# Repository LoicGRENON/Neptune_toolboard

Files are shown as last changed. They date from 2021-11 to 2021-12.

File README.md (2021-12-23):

# Neptune CAN Toolboard

A small controller board designed to be used on a 3D printer as well as a SMD Pick and Place (PNP) machine.
It is designed to be used with Klipper firmware using CAN bus or USB connection.
Using CAN bus is it possible to chain many board using a pair of twisted wires for data and power.
It is also a good solution to simplify the toolhead wiring as only one cable is needed.

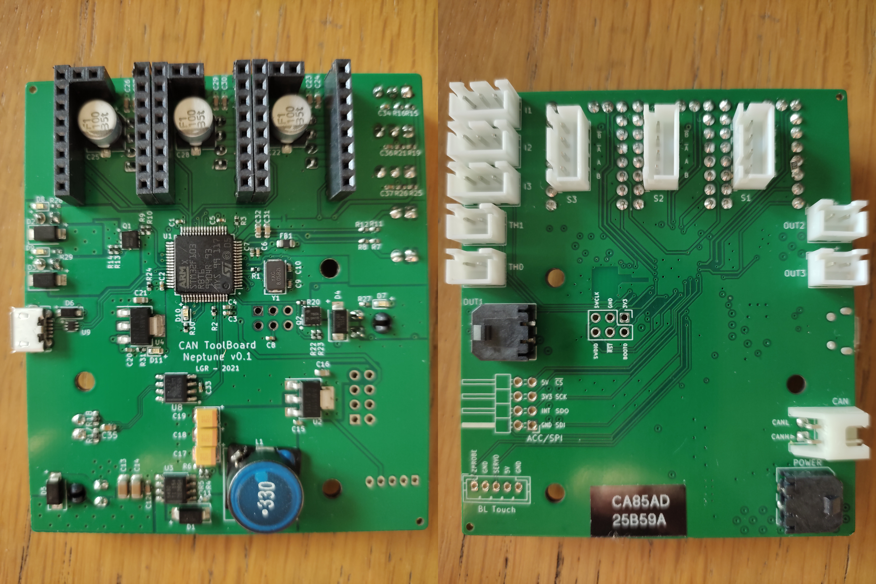
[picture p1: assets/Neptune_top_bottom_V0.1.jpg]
Neptune toolboard top and bottom sides


## Features:

* STM32F103 72MHz 32bits ARM MCU
* CAN bus
* USB (micro USB type B connector)
* 3x stepstick drivers with UART communication (with full diagnostics and control)
* 3x 5V powered inputs (endstop, filament runout sensor or whatever)
* 2x thermistor inputs (2.2k pullup resistor for PT1000 support)
* 3x MOSFET outputs (with freewheeling diode) - up to 5A
* 1x BL Touch connector
* 1x port for accelerometer connection for input shaping (no onboard chip as keeping the accelerometer as close to the nozzle is better)
* LEDs (Power, mosfet outputs & Activity)
* Debug port with SWD, NRST and BOOT0
* Components choosen for high-temp environnement (up to 85°C)

## Getting started:

To be defined

## Attribution

This board was designed from scratch but inspired by the [Huvud] and [TurboCAN] boards.

[Huvud]: https://github.com/bondus/KlipperToolboard
[TurboCAN]: https://github.com/henrikssn/TurboCAN

## License:
All included files are licensed under the [GNU GPL-3 license].

[GNU GPL-3 license]: https://www.gnu.org/licenses/gpl-3.0.html

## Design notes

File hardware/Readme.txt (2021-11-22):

kikit fab jlcpcb --assembly --schematic Toolboard/hardware_V6/TriStepToolboard.sch Toolboard/hardware_V6/TriStepToolboard.kicad_pcb Toolboard/hardware_V6/assembly

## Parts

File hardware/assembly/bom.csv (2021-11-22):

Comment | Designator | Footprint | LCSC
Debug | J1 | Connector_PinHeader_2.54mm:PinHeader_2x03_P2.54mm_Vertical | ---
12p | C9,C10 | Capacitor_SMD:C_0402_1005Metric | C1547
10k | R2,R3,R4,R8,R12,R10,R14,R22,R29,R28,R27,R19,R21,R15,R16,R25,R26 | Resistor_SMD:R_0402_1005Metric | C25744
0.1u | C8,C3,C1,C5,C2,C36,C34,C33,C37 | Capacitor_SMD:C_0402_1005Metric | C1525
Net-Tie_GND_GNDA | NT1 | NetTie:NetTie-2_SMD_Pad0.5mm | ---
1u | C7 | Capacitor_SMD:C_0402_1005Metric | C52923
4.7u | C4,C15,C20 | Capacitor_SMD:C_0402_1005Metric | C23733
10n | C6,C11 | Capacitor_SMD:C_0402_1005Metric | C15195
600 @ 100MHz | FB1 | Inductor_SMD:L_0805_2012Metric | C1017
0 | R1 | Resistor_SMD:R_0402_1005Metric | C17168
8MHz | Y1 | Crystal:Crystal_SMD_5032-2Pin_5.0x3.2mm | C115962
STM32F103R8Tx | U1 | Package_QFP:LQFP-64_10x10mm_P0.5mm | ---
AMS1117-5.0 | U2 | Package_TO_SOT_SMD:SOT-223-3_TabPin2 | C6187
22u | C16,C21 | Capacitor_SMD:C_0603_1608Metric | C59461
AMS1117-3.3 | U4 | Package_TO_SOT_SMD:SOT-223-3_TabPin2 | C6186
SS54 | D1,D5,D2,D3,D4 | Diode_SMD:D_SMA | C22452
33u | L1 | Inductor_SMD:L_12x12mm_H8mm | C87568
TPS5430DDAR | U3 | Package_SO:TI_SO-PowerPAD-8_ThermalVias | C9864
10u | C14,C13 | Capacitor_SMD:C_1206_3216Metric | C13585
0.1u | C12,C26,C29,C23,C24,C27,C30 | Capacitor_SMD:C_0603_1608Metric | C14663
1k | R5 | Resistor_SMD:R_0402_1005Metric | C11702
22u | C17,C18,C19 | Capacitor_Tantalum_SMD:CP_EIA-3528-15_AVX-H | C308917
100 | R6 | Resistor_SMD:R_0402_1005Metric | C25076
TMC2209StepStick | U5,U6,U7 | project:TMC2209StepStick | ~
Stepper1 | J2 | Connector_JST:JST_XH_B4B-XH-A_1x04_P2.50mm_Vertical | ---
100uF | C25,C28,C22 | Capacitor_SMD:CP_Elec_6.3x5.8 | C249982
Stepper2 | J3 | Connector_JST:JST_XH_B4B-XH-A_1x04_P2.50mm_Vertical | ---
Stepper3 | J4 | Connector_JST:JST_XH_B4B-XH-A_1x04_P2.50mm_Vertical | ---
GN | D10,D11,D9,D8,D7 | LED_SMD:LED_0603_1608Metric | C72043
470 | R30,R31 | Resistor_SMD:R_0402_1005Metric | C25117
1.5k | R24 | Resistor_SMD:R_0402_1005Metric | C25867
2.2k 0.1% | R7,R11 | Resistor_SMD:R_0402_1005Metric | C186333
2.2u | C31,C32 | Capacitor_SMD:C_0603_1608Metric | C23630
TH0 | J6 | Connector_JST:JST_XH_B2B-XH-A_1x02_P2.50mm_Vertical | ---
TH1 | J7 | Connector_JST:JST_XH_B2B-XH-A_1x02_P2.50mm_Vertical | ---
22 | R9,R13,R20,R23 | Resistor_SMD:R_0402_1005Metric | C25092
FAN0 | J5 | Connector_JST:JST_XH_B2B-XH-A_1x02_P2.50mm_Vertical | ---
FAN1 | J8 | Connector_JST:JST_XH_B2B-XH-A_1x02_P2.50mm_Vertical | ---
HEAT | J11 | Connector_Molex:Molex_Micro-Fit_3.0_43650-0200_1x02_P3.00mm_Horizontal | ---
AON7804 | Q1,Q2 | project:DFN3X3A_Dual | C431197
BL_Touch | J16 | Connector_JST:JST_PH_B5B-PH-K_1x05_P2.00mm_Vertical | ---
Conn_01x03 | J12,J9,J15 | Connector_JST:JST_XH_B3B-XH-A_1x03_P2.50mm_Vertical | ---
PWR | J13 | Connector_Molex:Molex_Micro-Fit_3.0_43650-0200_1x02_P3.00mm_Horizontal | ---
USB_B_Micro | J14 | Connector_USB:USB_Micro-B_Molex-105017-0001 | C10418
USBLC6-2P6 | U9 | Package_TO_SOT_SMD:SOT-666 | C15999
TCAN337DR | U8 | Package_SO:SOIC-8_3.9x4.9mm_P1.27mm | ---
CAN | J10 | Connector_JST:JST_XH_S2B-XH-A_1x02_P2.50mm_Horizontal | ---
B5819W SL | D6 | Diode_SMD:D_SOD-123 | C8598
MountingHole | H1,H2,H3 | MountingHole:MountingHole_3.2mm_M3 | ---
SPI | J17 | Connector_PinHeader_2.54mm:PinHeader_2x04_P2.54mm_Horizontal | ---
60 | R17,R18 | Resistor_SMD:R_0603_1608Metric | C166918
4.7n | C35 | Capacitor_SMD:C_0603_1608Metric | C53987

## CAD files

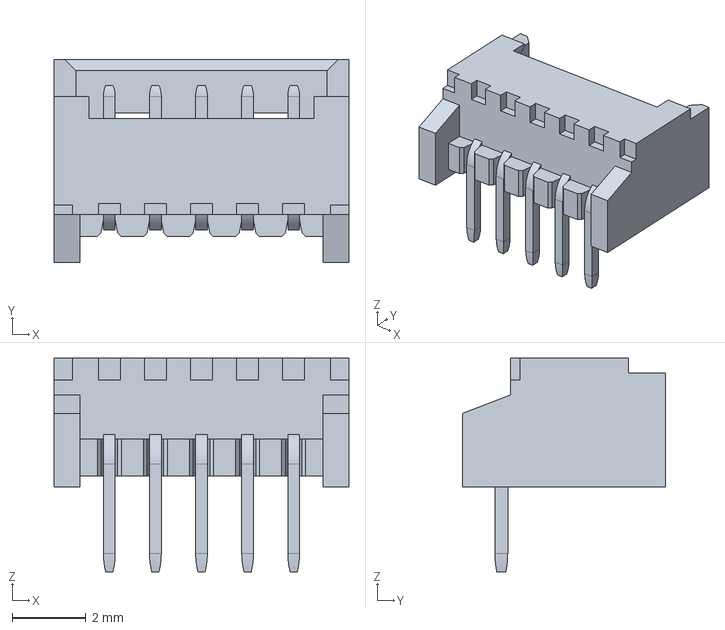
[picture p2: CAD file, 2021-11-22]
hardware/step files/Molex_530480510.stp
8.00 x 5.50 x 5.80 mm

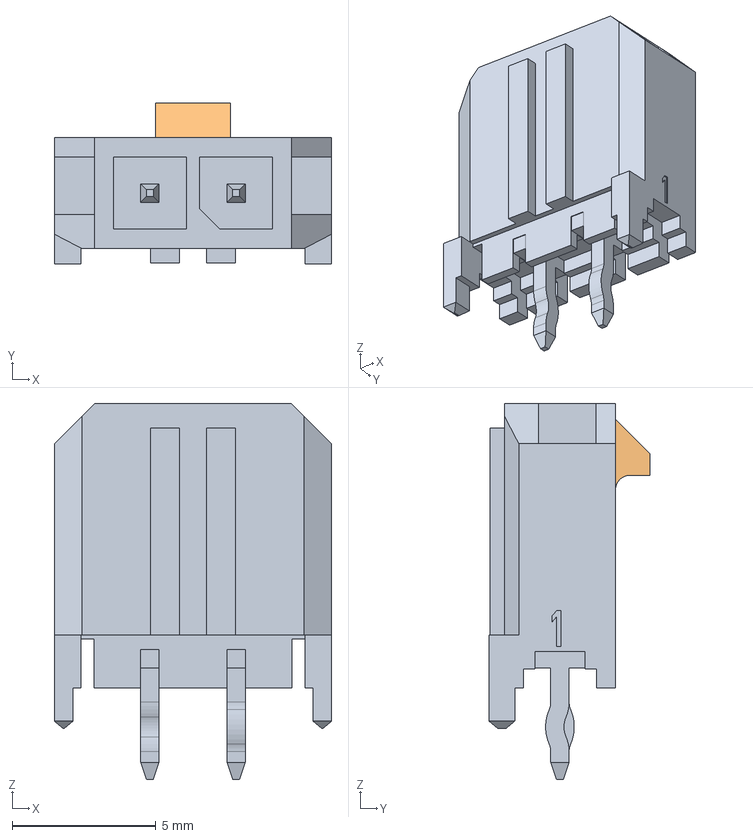
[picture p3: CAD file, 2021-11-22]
hardware/step files/Molex_436500215.stp
9.65 x 5.61 x 13.1 mm

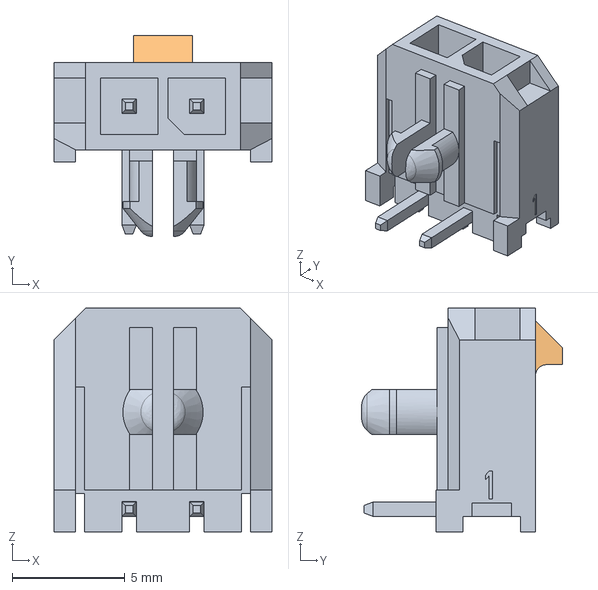
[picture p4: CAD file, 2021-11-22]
hardware/step files/Molex_436500200.stp
9.65 x 8.90 x 9.90 mm

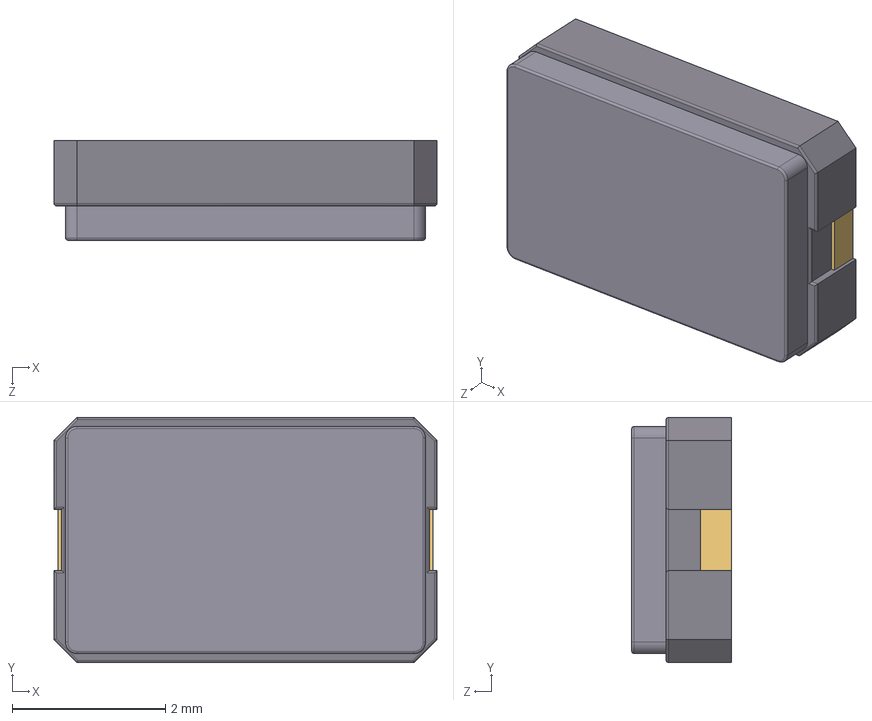
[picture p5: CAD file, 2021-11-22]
hardware/step files/Cystal_5032.step
5.00 x 3.20 x 1.30 mm

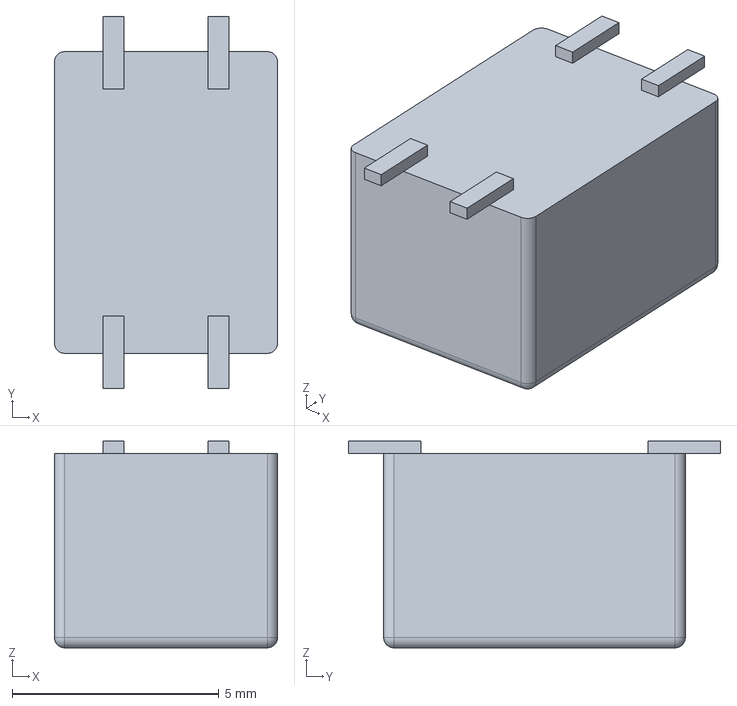
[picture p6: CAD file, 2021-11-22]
hardware/step files/dr331.stp
5.40 x 9.00 x 5.00 mm

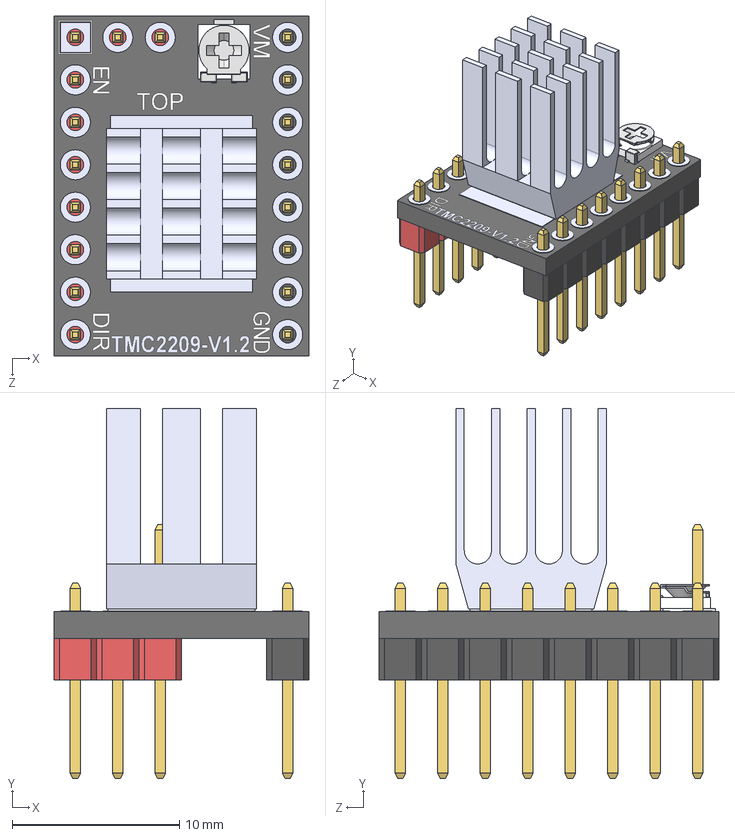
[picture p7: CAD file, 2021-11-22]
hardware/step files/TMC2209-V1.2.STEP
15.2 x 22.1 x 20.3 mm
TMC2209_board^BTT TMC2209-V1.2(2)_BTT TMC2209-V1.2_DＧaut
Pin_Header_1x2_red^BTT TMC2209-V1.2(2)_BTT TMC2209-V1.2_DＧaut
Pin_Header_1x8_red^BTT TMC2209-V1.2(2)_BTT TMC2209-V1.2_DＧaut
Pin_Header_1x8_black^BTT TMC2209-V1.2(2)_BTT TMC2209-V1.2_DＧaut
EVM-3E___ _________^BTT TMC2209-V1.2(2)_BTT TMC2209-V1.2_DＧaut
TMC2209_heatsink^BTT TMC2209-V1.2(2)_BTT TMC2209-V1.2_DＧaut

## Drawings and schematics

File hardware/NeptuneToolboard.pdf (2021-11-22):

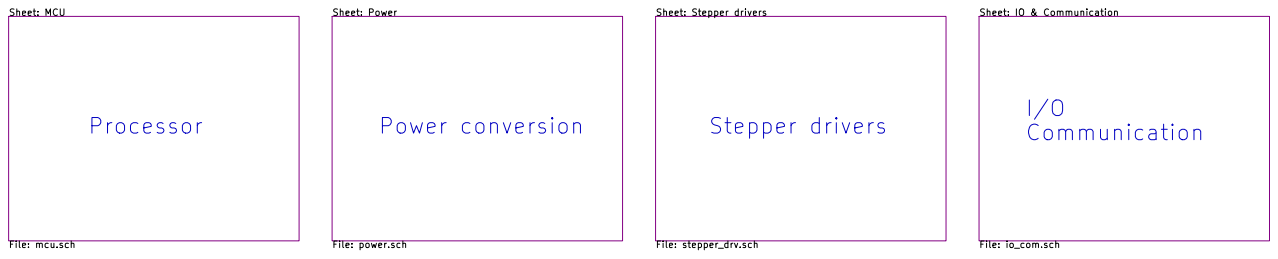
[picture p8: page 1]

File: TriStepToolboard.sch Sheet: / LGR

Id: 1/5 Title: Tri-steppers CAN Tool Board

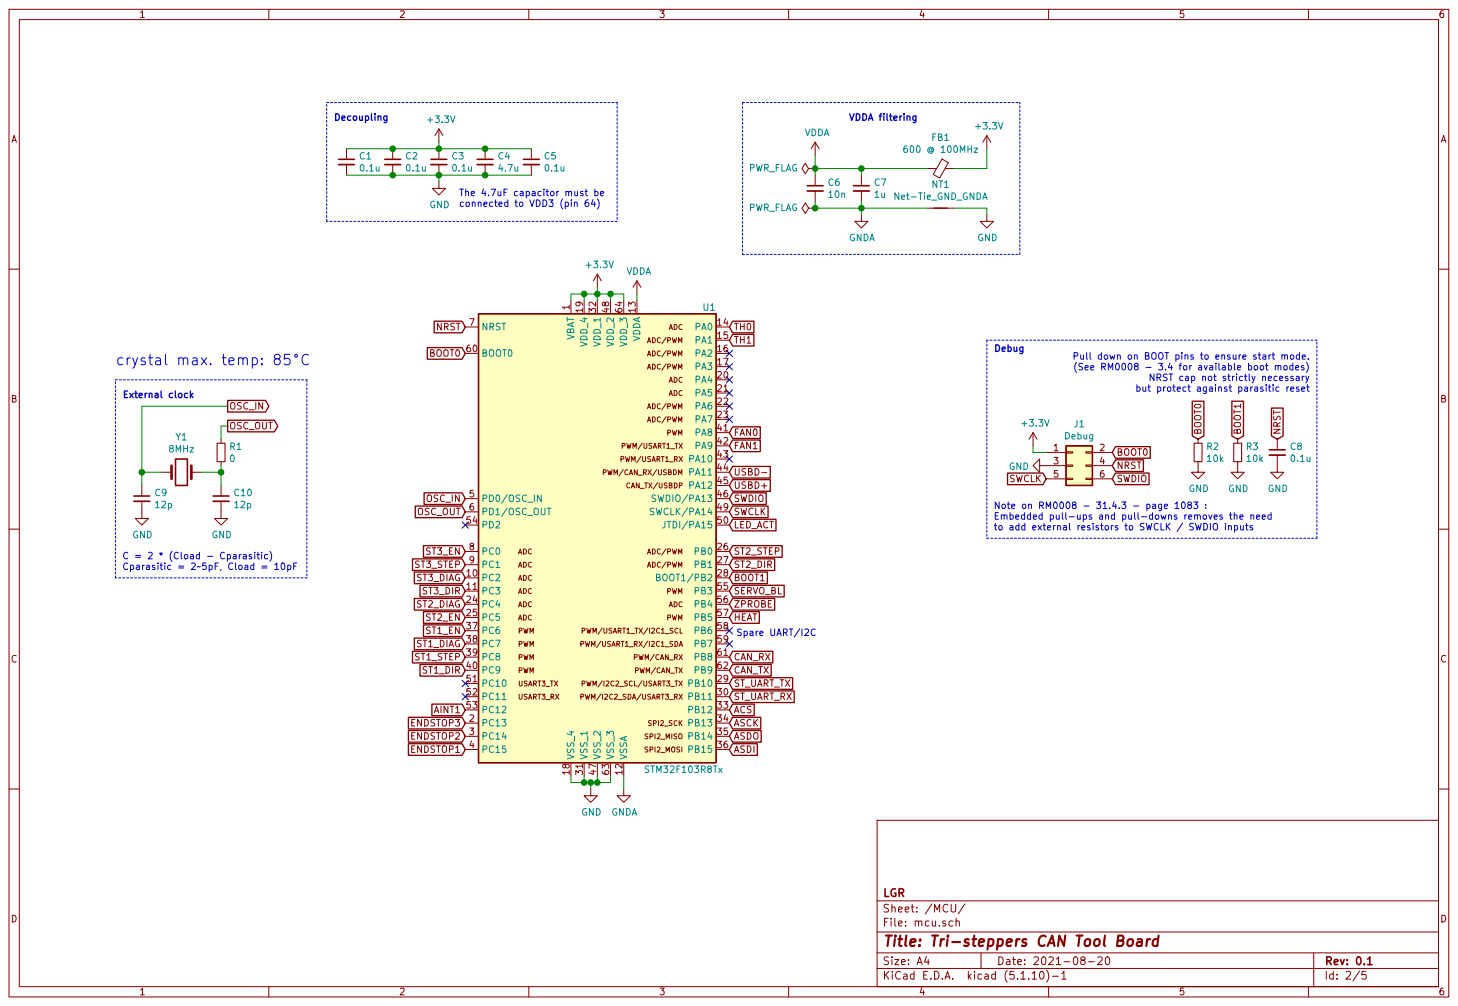
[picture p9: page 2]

1 PC2 10 PC3 11 VSSA 12 VDDA 13 PA0 14 PA1 15 PA2 16 PA3 17 VSS_4 18 VDD_4 19 PC13 2 PA4 20 PA5 21 PA6 22 PA7 23 PC4 24 PC5 25 PB0 26 PB1 27 BOOT1/PB2 28 PB10 29 PC14 3 PB11 30 VSS_1 31 VDD_1 32 PB12 33 PB13 34 PB14 35 PB15 36 PC6 37 PC7 38 PC8 39 PC15 4 PC9 40 PA8 41 PA9 42 PA10 43 PA11 44 PA12 45 SWDIO/PA13 46 VSS_2 47 VDD_2 48 SWCLK/PA14 49 PD0/OSC_IN 5

Pull down on BOOT pins to ensure start mode.
(See RM0008 - 3.4 for available boot modes)

NRST cap not strictly necessary
but protect against parasitic reset

Note on RM0008 - 31.4.3 - page 1083 :
Embedded pull-ups and pull-downs removes the need
to add external resistors to SWCLK / SWDIO inputs

File: mcu.sch Sheet: /MCU/ LGR

Id: 2/5 Title: Tri-steppers CAN Tool Board

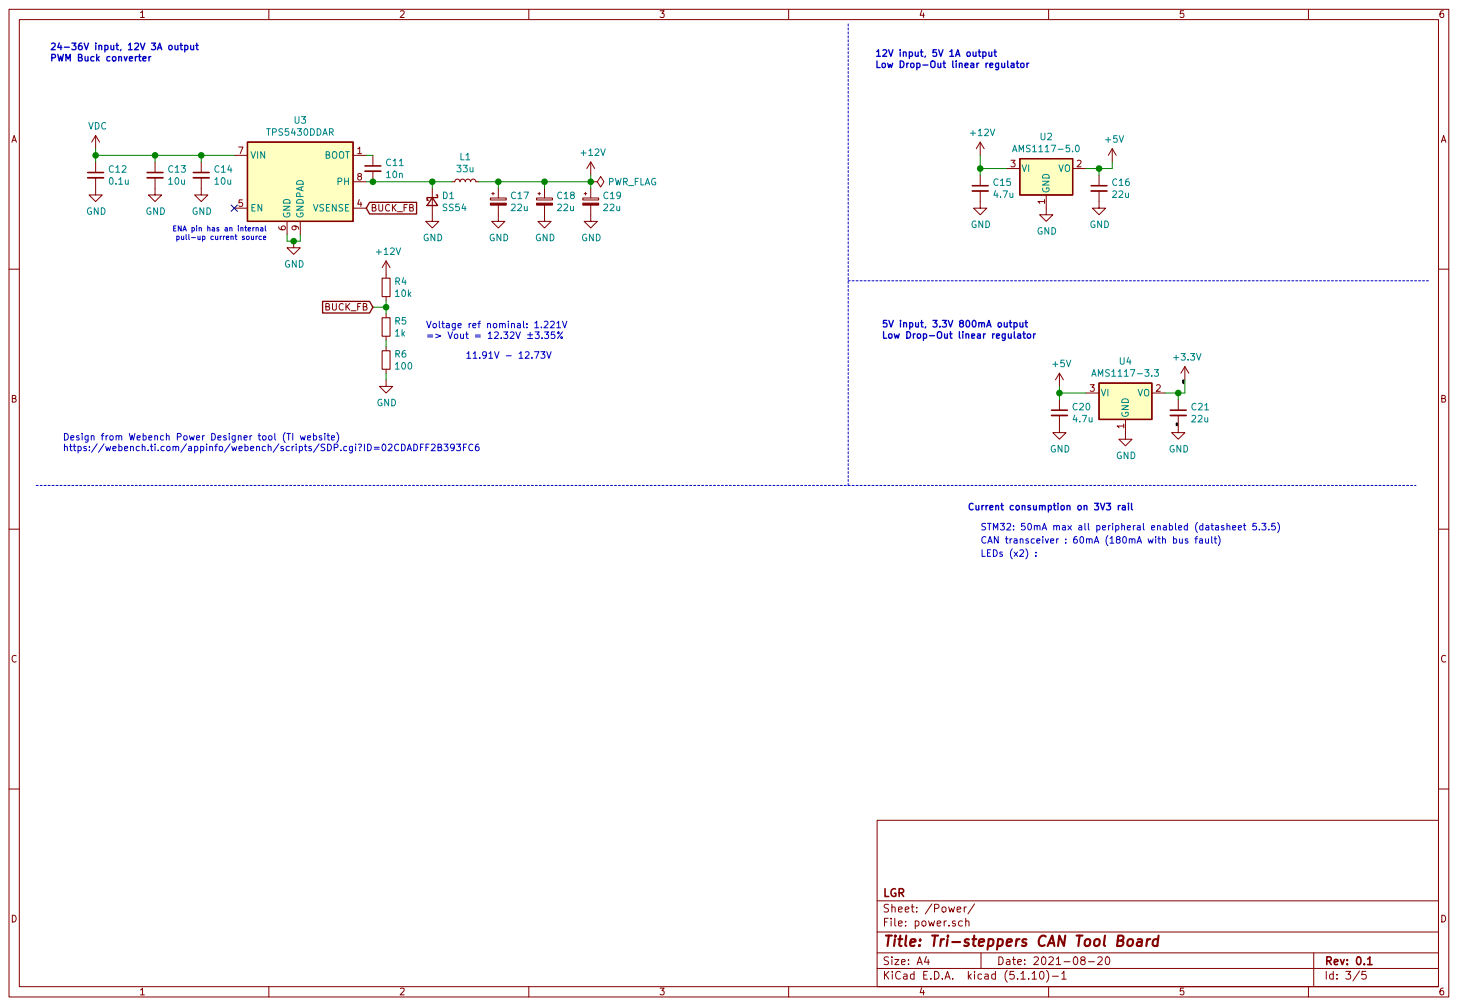
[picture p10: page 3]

12V input, 5V 1A output
Low Drop-Out linear regulator

1 VO 2 VI 3 U4 AMS1117-3.3 GND GND GND

Design from Webench Power Designer tool (TI website)
https://webench.ti.com/appinfo/webench/scripts/SDP.cgi?ID=02CDADFF2B393FC6

Current consumption on 3V3 rail
STM32: 50mA max all peripheral enabled (datasheet 5.3.5)

File: power.sch Sheet: /Power/ LGR

Id: 3/5 Title: Tri-steppers CAN Tool Board

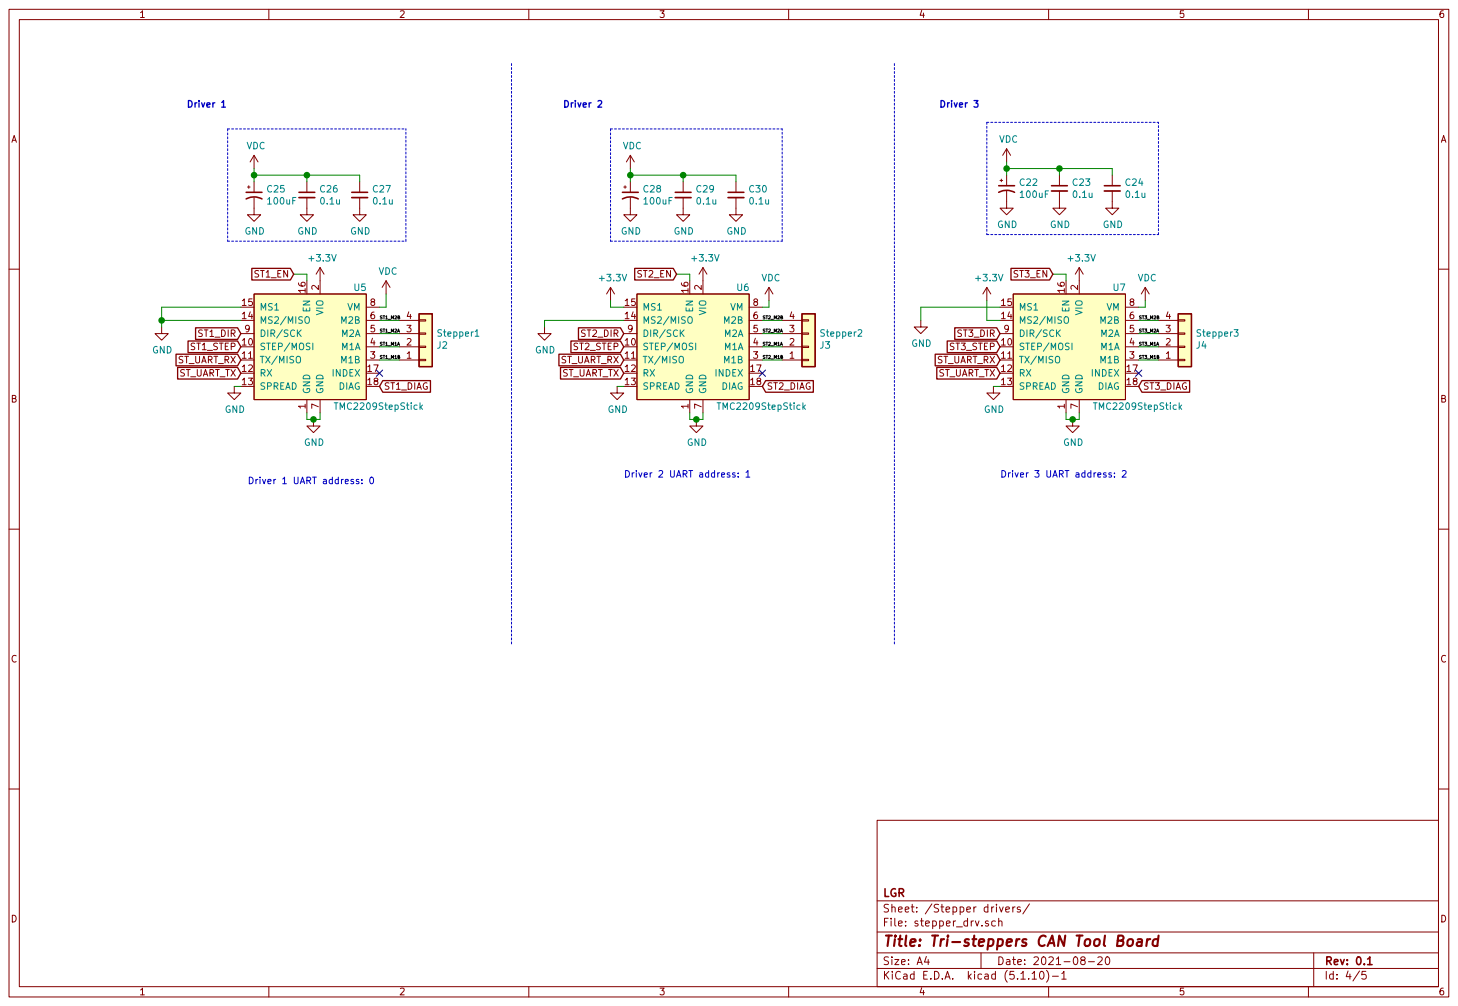
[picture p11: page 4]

7 VM 8 DIR/SCK 9 U6 TMC2209StepStick GND GND GND GND

7 VM 8 DIR/SCK 9 U5 GND TMC2209StepStick GND GND

1 STEP/MOSI 10 TX/MISO 11 RX 12 SPREAD 13 MS2/MISO 14 MS1 15 EN 16

7 VM 8 DIR/SCK 9 U7 TMC2209StepStick GND

Sheet: /Stepper drivers/ LGR

File: stepper_drv.sch
Id: 4/5 Title: Tri-steppers CAN Tool Board

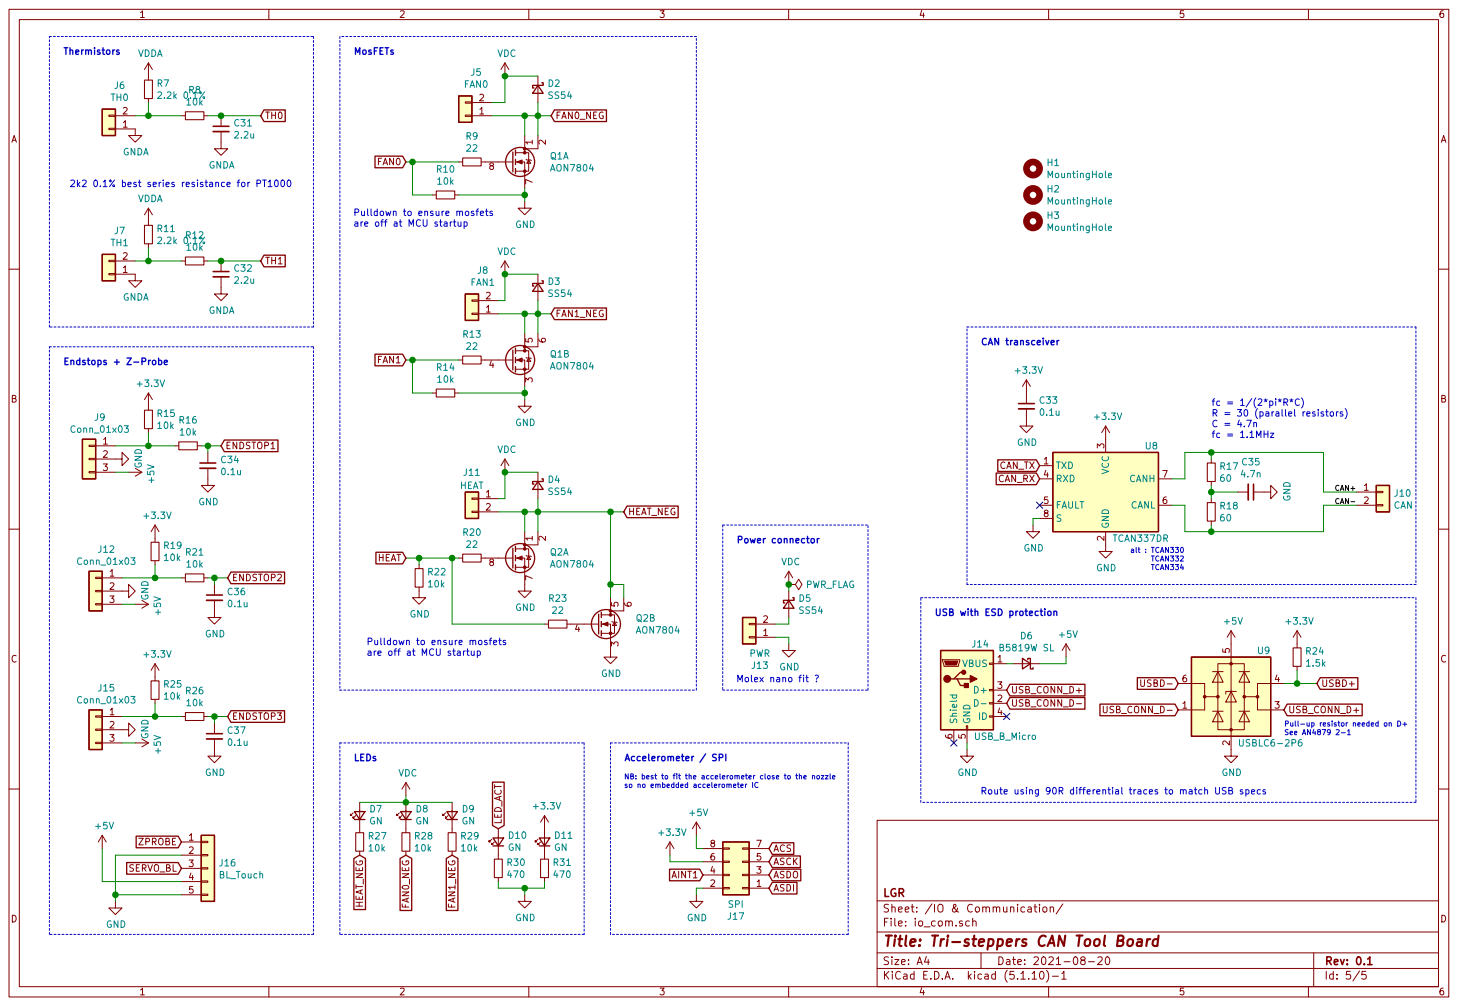
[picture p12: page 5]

CAN+ CAN- Pulldown to ensure mosfets are off at MCU startup

3 RXD 4 FAULT 5 CANL 6 CANH 7 S

so no embedded accelerometer IC

File: io_com.sch Sheet: /IO & Communication/ LGR

Id: 5/5 Title: Tri-steppers CAN Tool Board

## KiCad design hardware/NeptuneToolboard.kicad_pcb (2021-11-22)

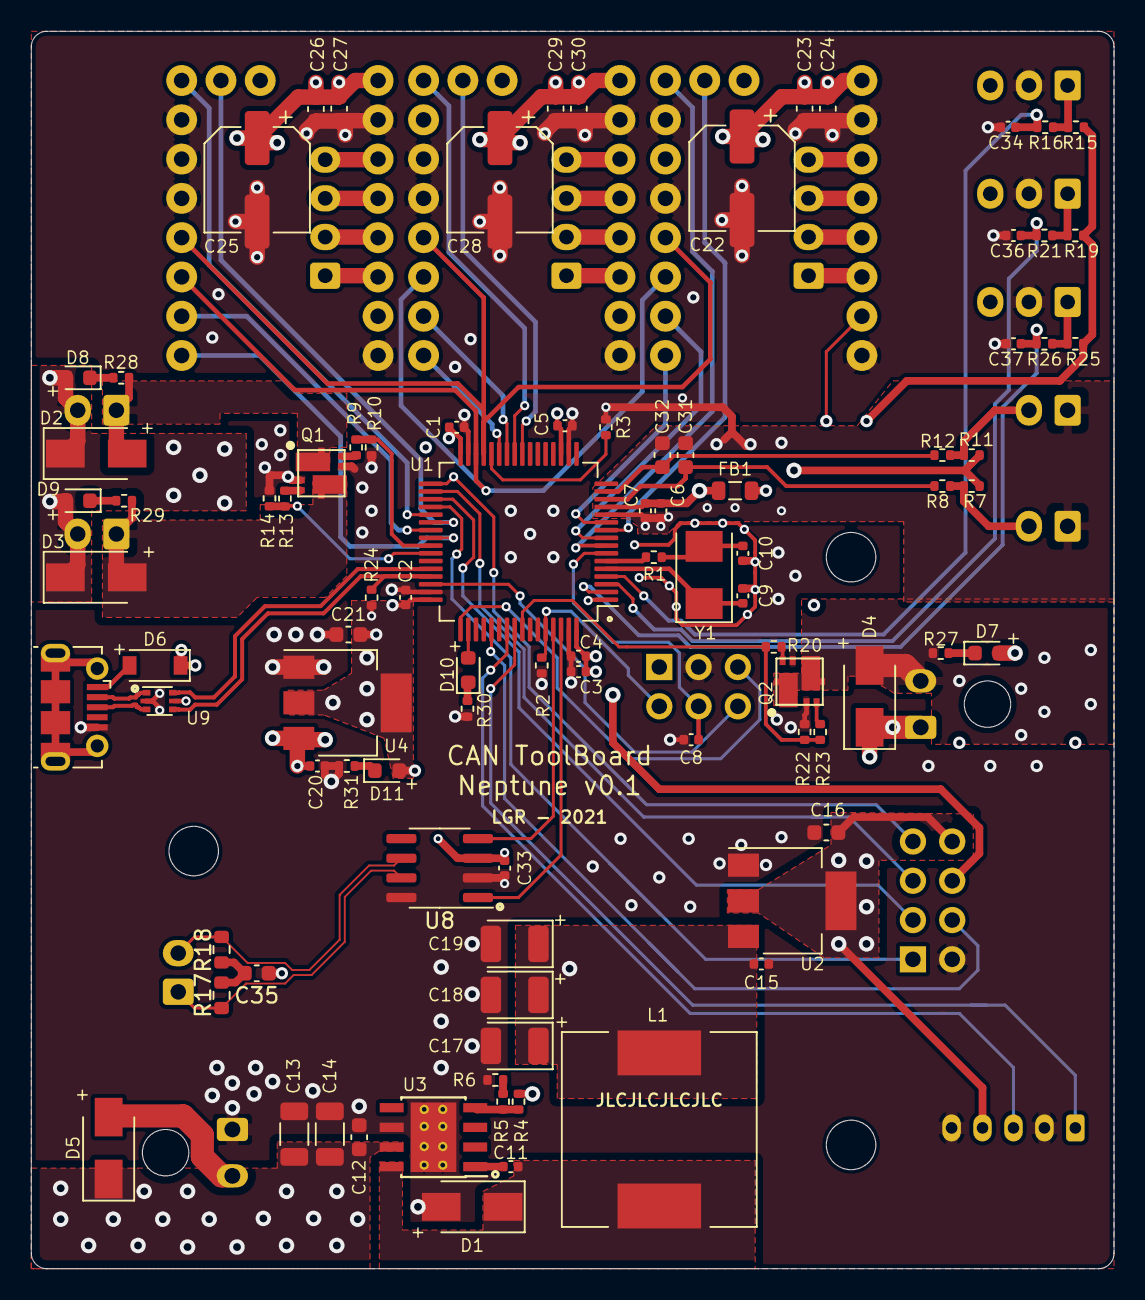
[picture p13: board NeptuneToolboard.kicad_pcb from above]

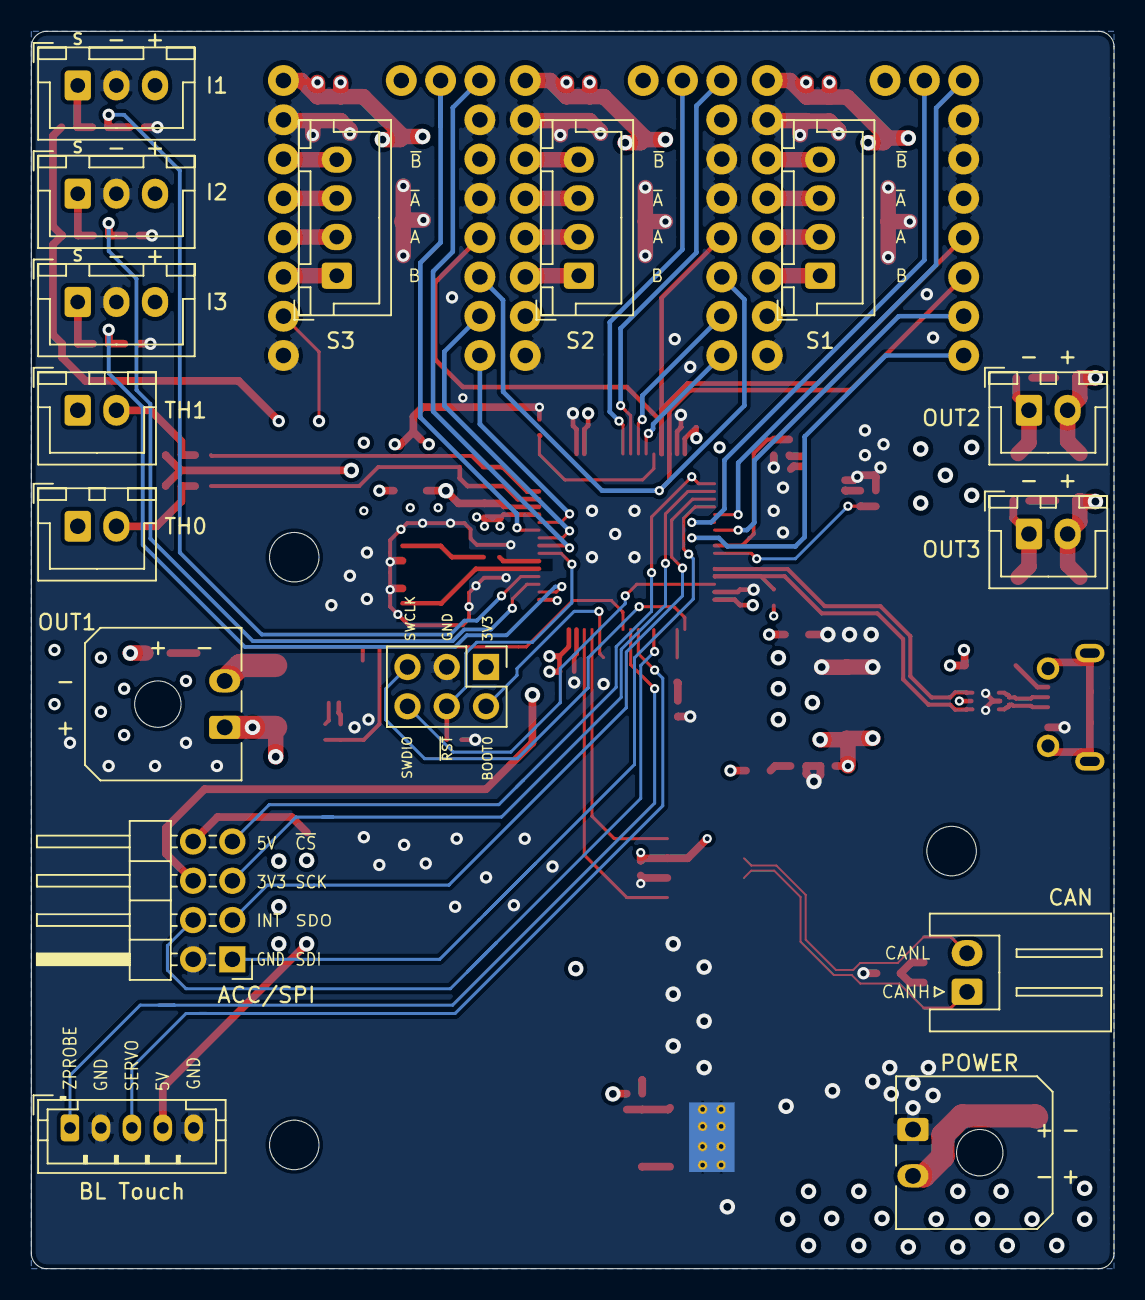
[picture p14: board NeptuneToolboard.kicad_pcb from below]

Board: 4 copper layers, 70.0 x 80.0 mm, 114 parts (16 on the bottom side), 89 nets.

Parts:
C1, C2, C3, C5, C8, C33, C34, C36, C37: 0.1u; C_0402_1005Metric
C4, C15, C20: 4.7u; C_0402_1005Metric
C6, C11: 10n; C_0402_1005Metric
C7: 1u; C_0402_1005Metric
C9, C10: 12p; C_0402_1005Metric
C12, C23, C24, C26, C27, C29, C30: 0.1u; C_0603_1608Metric
C13, C14: 10u; C_1206_3216Metric
C16, C21: 22u; C_0603_1608Metric
C17, C18, C19: 22u; CP_EIA-3528-15_AVX-H
C22, C25, C28: 100uF; CP_Elec_6.3x5.8
C31, C32: 2.2u; C_0603_1608Metric
C35: 4.7n; C_0603_1608Metric
D1, D2, D3, D4, D5: SS54; D_SMA
D6: B5819W SL; D_SOD-123
D7, D8, D9, D10, D11: GN; LED_0603_1608Metric
FB1: 600 @ 100MHz; L_0805_2012Metric
H1, H2, H3: MountingHole; MountingHole_3.2mm_M3
J1: Debug; PinHeader_2x03_P2.54mm_Vertical
J2: Stepper1; JST_XH_B4B-XH-A_1x04_P2.50mm_Vertical
J3: Stepper2; JST_XH_B4B-XH-A_1x04_P2.50mm_Vertical
J4: Stepper3; JST_XH_B4B-XH-A_1x04_P2.50mm_Vertical
J5: FAN0; JST_XH_B2B-XH-A_1x02_P2.50mm_Vertical
J6: TH0; JST_XH_B2B-XH-A_1x02_P2.50mm_Vertical
J7: TH1; JST_XH_B2B-XH-A_1x02_P2.50mm_Vertical
J8: FAN1; JST_XH_B2B-XH-A_1x02_P2.50mm_Vertical
J9, J12, J15: Conn_01x03; JST_XH_B3B-XH-A_1x03_P2.50mm_Vertical
J10: CAN; JST_XH_S2B-XH-A_1x02_P2.50mm_Horizontal
J11: HEAT; Molex_Micro-Fit_3.0_43650-0200_1x02_P3.00mm_Horizontal
J13: PWR; Molex_Micro-Fit_3.0_43650-0200_1x02_P3.00mm_Horizontal
J14: USB_B_Micro; USB_Micro-B_Molex-105017-0001
J16: BL_Touch; JST_PH_B5B-PH-K_1x05_P2.00mm_Vertical
J17: SPI; PinHeader_2x04_P2.54mm_Horizontal
L1: 33u; L_12x12mm_H8mm
NT1: Net-Tie_GND_GNDA; NetTie-2_SMD_Pad0.5mm
Q1, Q2: AON7804; DFN3X3A_Dual
R1: 0; R_0402_1005Metric
R2, R3, R4, R8, R10, R12, R14, R15, R16, R19, R21, R22, R25, R26, R27, R28, R29: 10k; R_0402_1005Metric
R5: 1k; R_0402_1005Metric
R6: 100; R_0402_1005Metric
R7, R11: 2.2k 0.1%; R_0402_1005Metric
R9, R13, R20, R23: 22; R_0402_1005Metric
R17, R18: 60; R_0603_1608Metric
R24: 1.5k; R_0402_1005Metric
R30, R31: 470; R_0402_1005Metric
U1: STM32F103R8Tx; LQFP-64_10x10mm_P0.5mm
U2: AMS1117-5.0; SOT-223-3_TabPin2
U3: TPS5430DDAR; TI_SO-PowerPAD-8_ThermalVias
U4: AMS1117-3.3; SOT-223-3_TabPin2
U5, U6, U7: TMC2209StepStick
U8: TCAN337DR; SOIC-8_3.9x4.9mm_P1.27mm
U9: USBLC6-2P6; SOT-666
Y1: 8MHz; Crystal_SMD_5032-2Pin_5.0x3.2mm

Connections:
+3V3: C1.1, C2.1, C3.1, C4.1, C5.1, C21.1, C33.1, D11.2, FB1.1, J1.1, J17.6, R15.1, R19.1, R24.1, R25.1, U1.1, U1.19, U1.32, U1.48, U1.64, U4.2, U5.2, U6.2, U6.15, U7.2, U7.14, U8.3
+5V: C16.1, C20.1, D6.1, J9.3, J12.3, J15.3, J16.4, J17.8, U2.2, U4.3, U9.5
+12V: C15.1, C17.1, C18.1, C19.1, L1.2, R4.1, U2.3
/IO & Communication/CAN+: J10.1, R17.1, U8.7
/IO & Communication/CAN-: J10.2, R18.2, U8.6
/Stepper drivers/ST1_M1A: J2.2, U5.4
/Stepper drivers/ST1_M1B: J2.1, U5.3
/Stepper drivers/ST1_M2A: J2.3, U5.5
/Stepper drivers/ST1_M2B: J2.4, U5.6
/Stepper drivers/ST2_M1A: J3.2, U6.4
/Stepper drivers/ST2_M1B: J3.1, U6.3
/Stepper drivers/ST2_M2A: J3.3, U6.5
/Stepper drivers/ST2_M2B: J3.4, U6.6
/Stepper drivers/ST3_M1A: J4.2, U7.4
/Stepper drivers/ST3_M1B: J4.1, U7.3
/Stepper drivers/ST3_M2A: J4.3, U7.5
/Stepper drivers/ST3_M2B: J4.4, U7.6
ACS: J17.7, U1.33
AINT1: J17.4, U1.53
ASCK: J17.5, U1.34
ASDI: J17.1, U1.36
ASDO: J17.3, U1.35
BOOT0: J1.2, R2.1, U1.60
BOOT1: R3.1, U1.28
BUCK_FB: R4.2, R5.1, U3.4
CAN_RX: U1.61, U8.4
CAN_TX: U1.62, U8.1
ENDSTOP1: C34.1, R16.1, U1.4
ENDSTOP2: C36.1, R21.1, U1.3
ENDSTOP3: C37.1, R26.1, U1.2
FAN0: R9.2, R10.2, U1.41
FAN0_NEG: D2.2, J5.1, Q1.1, Q1.2, R28.2
FAN1: R13.2, R14.2, U1.42
FAN1_NEG: D3.2, J8.1, Q1.5, Q1.6, R29.2
GND: C1.2, C2.2, C3.2, C4.2, C5.2, C8.2, C9.2, C10.2, C12.2, C13.2, C14.2, C15.2, C16.2, C17.2, C18.2, C19.2, C20.2, C21.2, C22.2, C23.2, C24.2, C25.2, C26.2, C27.2, C28.2, C29.2, C30.2, C33.2, C34.2, C35.1, C36.2, C37.2, D1.2, J1.3, J9.2, J12.2, J13.1, J14.5, J15.2, J16.2, J16.5, J17.2, NT1.2, Q1.3, Q1.7, Q2.3, Q2.7, R2.2, R3.2, R6.2, R10.1, R14.1, R22.2, R30.2, R31.2, U1.18, U1.31, U1.47, U1.63, U2.1, U3.6, U3.9, U4.1, U5.1, U5.7, U5.13, U5.14, U5.15, U6.1, U6.7, U6.13, U6.14, U7.1, U7.7, U7.13, U7.15, U8.2, U8.8, U9.2
GNDA: C6.2, C7.2, C31.2, C32.2, J6.1, J7.1, NT1.1, U1.12
HEAT: R20.2, R22.1, R23.2, U1.57
HEAT_NEG: D4.2, J11.2, Q2.1, Q2.2, Q2.5, Q2.6, R27.2
LED_ACT: D10.2, U1.50
NRST: C8.1, J1.4, U1.7
unnamed: C10.1, R1.2, Y1.2
unnamed: C11.1, U3.1
unnamed: C11.2, D1.1, L1.1, U3.8
unnamed: C35.2, R17.2, R18.1
unnamed: D5.2, J13.2
unnamed: D6.2, J14.1
unnamed: D7.1, R27.1
unnamed: D8.1, R28.1
unnamed: D9.1, R29.1
unnamed: D10.1, R30.1
unnamed: D11.1, R31.1
unnamed: J6.2, R7.2, R8.2
unnamed: J7.2, R11.2, R12.2
unnamed: J9.1, R15.2, R16.2
unnamed: J12.1, R19.2, R21.2
unnamed: J15.1, R25.2, R26.2
unnamed: Q1.4, R13.1
unnamed: Q1.8, R9.1
unnamed: Q2.4, R23.1
unnamed: Q2.8, R20.1
unnamed: R5.2, R6.1
OSC_IN: C9.1, U1.5, Y1.1
OSC_OUT: R1.1, U1.6
SERVO_BL: J16.3, U1.55
ST1_DIAG: U1.38, U5.18
ST1_DIR: U1.40, U5.9
ST1_EN: U1.37, U5.16
ST1_STEP: U1.39, U5.10
ST2_DIAG: U1.24, U6.18
ST2_DIR: U1.27, U6.9
ST2_EN: U1.25, U6.16
ST2_STEP: U1.26, U6.10
ST3_DIAG: U1.10, U7.18
ST3_DIR: U1.11, U7.9
ST3_EN: U1.8, U7.16
ST3_STEP: U1.9, U7.10
ST_UART_RX: U1.30, U5.11, U6.11, U7.11
ST_UART_TX: U1.29, U5.12, U6.12, U7.12
SWCLK: J1.5, U1.49
SWDIO: J1.6, U1.46
TH0: C31.1, R8.1, U1.14
TH1: C32.1, R12.1, U1.15
USBD+: R24.2, U1.45, U9.4
USBD-: U1.44, U9.6
USB_CONN_D+: J14.3, U9.3
USB_CONN_D-: J14.2, U9.1
VDC: C12.1, C13.1, C14.1, C22.1, C23.1, C24.1, C25.1, C26.1, C27.1, C28.1, C29.1, C30.1, D2.1, D3.1, D4.1, D5.1, D7.2, D8.2, D9.2, J5.2, J8.2, J11.1, U3.7, U5.8, U6.8, U7.8
VDDA: C6.1, C7.1, FB1.2, R7.1, R11.1, U1.13
ZPROBE: J16.1, U1.56

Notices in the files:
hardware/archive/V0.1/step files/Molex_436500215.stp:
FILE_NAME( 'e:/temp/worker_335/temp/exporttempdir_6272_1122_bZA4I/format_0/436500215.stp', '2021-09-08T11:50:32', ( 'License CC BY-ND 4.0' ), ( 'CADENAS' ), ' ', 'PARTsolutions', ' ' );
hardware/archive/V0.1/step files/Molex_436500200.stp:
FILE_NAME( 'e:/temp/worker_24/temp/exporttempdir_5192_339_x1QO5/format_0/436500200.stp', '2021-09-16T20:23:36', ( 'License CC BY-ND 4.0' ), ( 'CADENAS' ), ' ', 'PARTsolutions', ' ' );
